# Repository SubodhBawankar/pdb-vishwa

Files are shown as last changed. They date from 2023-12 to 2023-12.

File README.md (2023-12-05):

# pdb-vishwa
# Power Distribution Board for Vishwa Rover 2024

The circuitry converts voltage from batteries to a specific voltage using voltage regulators and switching regulators. Adjustable voltage converters are used to convert 12V to 5V, 3.7V, and 3.3V. Switching buck-boost converters are used to obtain 7V, 9V, and 24V from 12V. All this circuitry is integrated into a single Printed Circuit Board.

[Components List](https://docs.google.com/spreadsheets/d/1e5Fw-HEnwtgFm58ctA9HxLs7_NTRD_BNhpObLu1VbHM/edit?usp=sharing)

### Images: 
Connections:

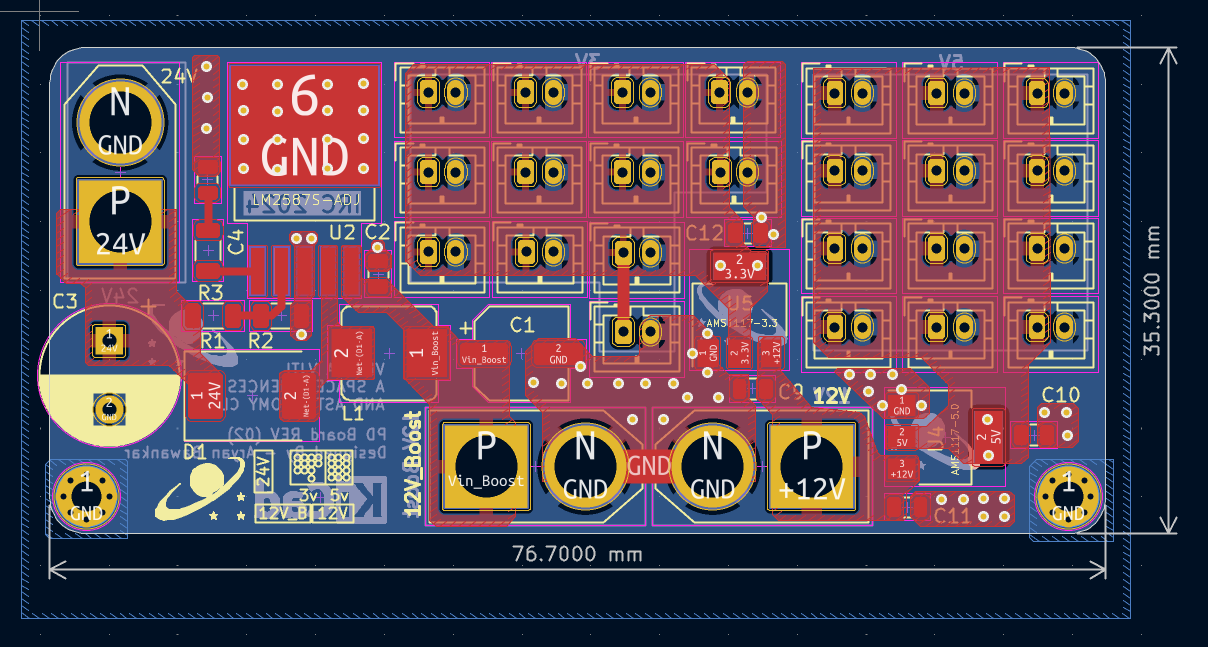
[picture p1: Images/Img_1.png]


3D View:

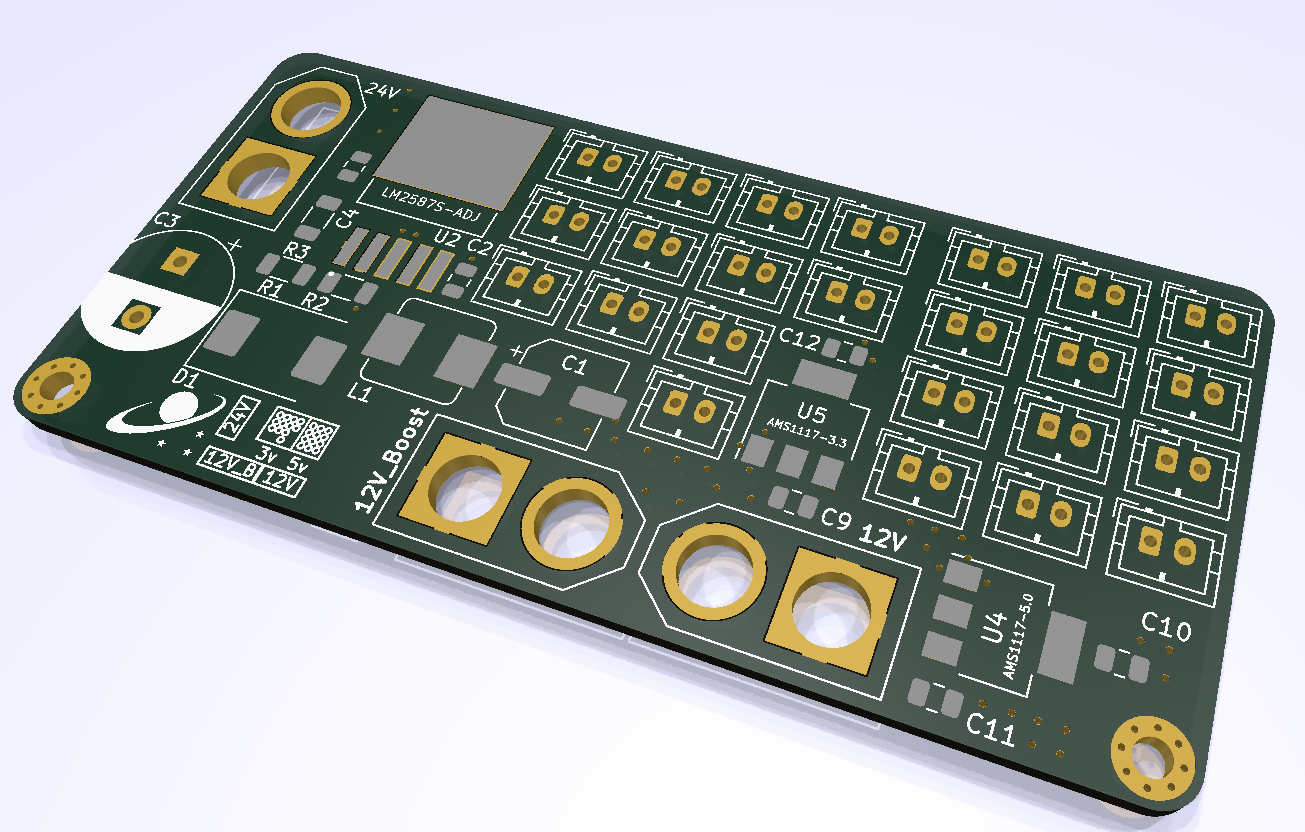
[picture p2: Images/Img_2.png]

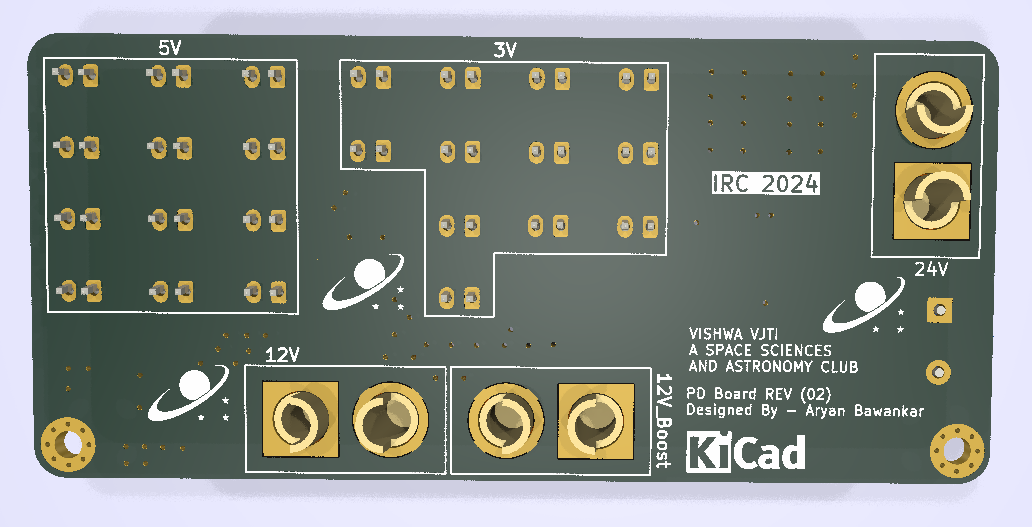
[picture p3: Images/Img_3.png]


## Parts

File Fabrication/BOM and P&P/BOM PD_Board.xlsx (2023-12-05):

Comment | Designator | Footprint | Quantity | JLCPCB Part # | Digikey Mgf #
2k | R2 | R_1206_3216Metric | 1 | C17944 | ESR18EZPF2001
33uH | L1 | L_Bourns_SRP7028A_7.3x6.6mm | 1 | C2046760 | SRP7028A-330M
36.9k | R1 | R_1206_3216Metric | 1 | C205346 | RC1206FR-0736K5L
AMS1117-3.3 | U5 | SOT-223-3_TabPin2 | 1 | C5250992 | 4518-AMS1117-3.3CT-ND
0.1uF | C2 | C_0805_2012Metric | 1 | C6641151 | C2012X7T2E104K125AE
0.68uF | C4 | C_0805_2012Metric | 1 | C520000 | C0805C684K5RAC7800
100uF | C1 | CP_Elec_6.3x7.7 | 1 | C5253633 | UCL1V101MCL6GS
1000uF | C3 | CP_Radial_D10.0mm_P5.00mm | 1 | C136014 | 35PX1000MEFC10X20
MBR745 | D1 | D_SMC | 1 | C524830 | SK56L-TP
10 uF | C11,C9,C10,C12 | C_0805_2012Metric | 4 | C162422 | GRM21BR61E106KA73L
3k | R3 | R_1206_3216Metric | 1 | C205286 | RC1206JR-073KL
AMS1117-5.0 | U4 | SOT-223-3_TabPin2 | 1 | C347223 | AZ1117IH-5.0TRG1
LM2587S-ADJ | U2 | VREG_TPS79625KTTR | 1 | C1355343 | LM2587SX-ADJ/NOPB
B2B-PH-K | P16,P19,P7,P24,P26,P13,P17,P21,P25,P23,P4,P22,P14,P28,P27,P2,P1,P5,P18,P3,P15,P20,P8,P6 | JST_PH_B2B-PH-K_1x02_P2.00mm_Vertical | 24 | C131337 | B2B-PH-K-S
XT60PW-M | J1,J2,J7 | AMASS_XT60-M | 3 | C98733 | PRT-10474
MountingHole_Pad | H2,H1 | MountingHole_2.2mm_M2_Pad_Via | 2

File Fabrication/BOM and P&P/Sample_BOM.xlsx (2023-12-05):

Comment | Designator | Footprint | JLCPCB Part #（optional）
100uF | C1 | CAP-SMD_L3.5-W2.8 | C16133
15K | R5,R6 | R0603 | C22809
DC-005-20A_C136744 | DC1 | DC-IN-TH_DC-005-20A | C136744
Header-Female-2.54_1x8 | P2,P3 | HDR-TH_8P-P2.54-V | C27438
K2-1102DP-C4SW-04 | SW1 | KEY-TH_4P-L6.0-W6.0-P4.50-LS6.5 | C110153
ATMEGA328P-PU | U1 | DIP-28_L34.6-W7.3-P2.54-LS10.2-BL | C33901
670688000 | USB1 | USB-B-TH_67068-8000 | C114097

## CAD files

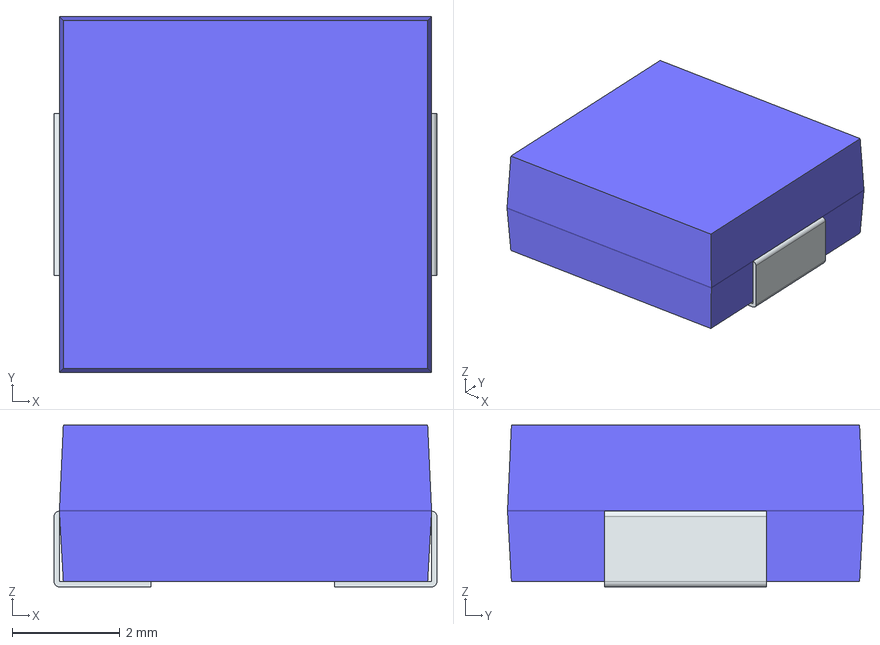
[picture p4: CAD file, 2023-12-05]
comps/22uH_IND/SRP7028AA-150M.stp
7.10 x 6.60 x 3.00 mm
FilletPin1
FilletPin2

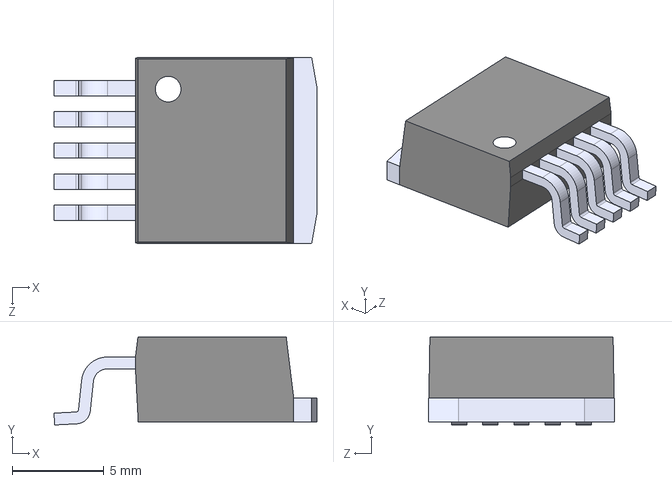
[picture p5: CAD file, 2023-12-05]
comps/LM2587S-ADJ/LM2587S-ADJ.step
14.4 x 4.80 x 10.2 mm

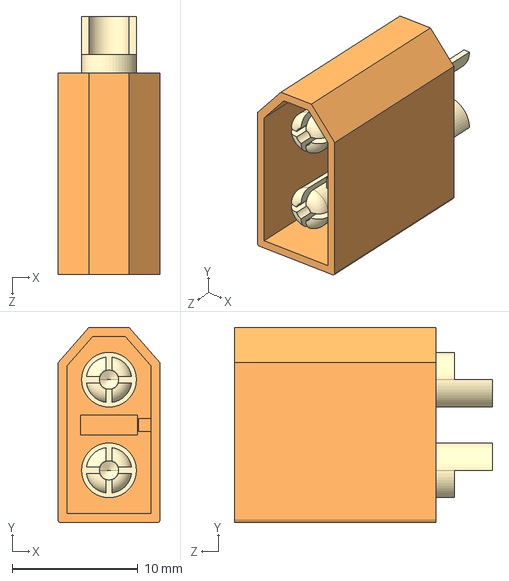
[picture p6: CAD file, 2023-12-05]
comps/XT60-M/XT60-M.step
8.10 x 15.5 x 20.5 mm

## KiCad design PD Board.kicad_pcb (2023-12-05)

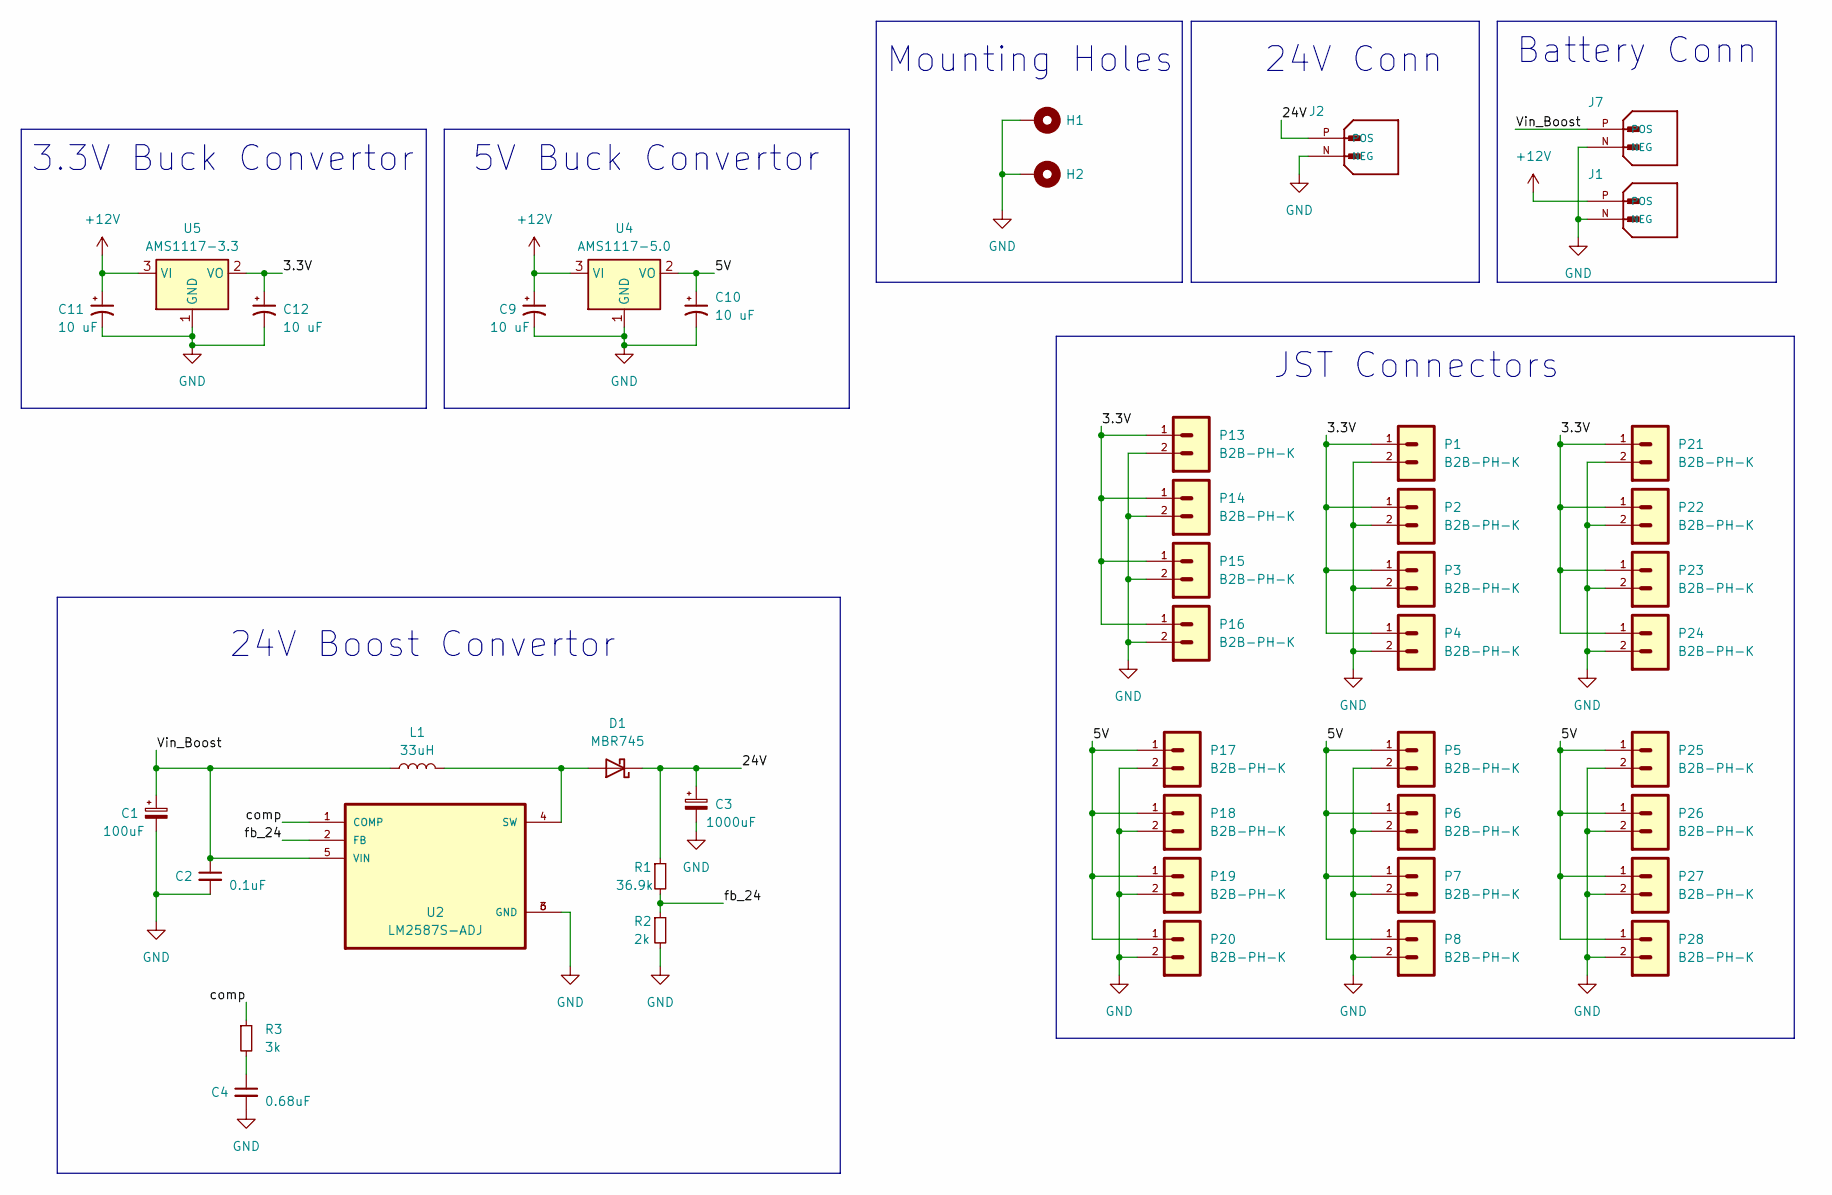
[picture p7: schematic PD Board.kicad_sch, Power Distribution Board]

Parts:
C1: 100uF; CP_Elec_6.3x7.7
C2: 0.1uF; C_0805_2012Metric
C3: 1000uF; CP_Radial_D10.0mm_P5.00mm
C4: 0.68uF; C_0805_2012Metric
C9, C10, C11, C12: 10 uF; C_0805_2012Metric
D1: MBR745; D_SMC
H1, H2: MountingHole_Pad; MountingHole_2.2mm_M2_Pad_Via
J1, J2, J7: XT60PW-M; AMASS_XT60-M; PARTREV V1.2
L1: 33uH; L_Bourns_SRP7028A_7.3x6.6mm
P1, P2, P3, P4, P5, P6, P7, P8, P13, P14, P15, P16, P17, P18, P19, P20, P21, P22, P23, P24, P25, P26, P27, P28: B2B-PH-K; JST_PH_B2B-PH-K_1x02_P2.00mm_Vertical
R1: 36.9k; R_1206_3216Metric
R2: 2k; R_1206_3216Metric
R3: 3k; R_1206_3216Metric
U2: LM2587S-ADJ; VREG_TPS79625KTTR
U4: AMS1117-5.0; SOT-223-3_TabPin2
U5: AMS1117-3.3; SOT-223-3_TabPin2

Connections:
+12V: C9.1, C11.1, J1.P (POS), U4.3 (VI), U5.3 (VI)
/3.3V: C12.1, P1.1, P2.1, P3.1, P4.1, P13.1, P14.1, P15.1, P16.1, P21.1, P22.1, P23.1, P24.1, U5.2 (VO)
/5V: C10.1, P5.1, P6.1, P7.1, P8.1, P17.1, P18.1, P19.1, P20.1, P25.1, P26.1, P27.1, P28.1, U4.2 (VO)
/24V: C3.1, D1.1 (K), J2.P (POS), R1.1
/Vin_Boost: C1.1, C2.1, J7.P (POS), L1.1, U2.5 (VIN)
/comp: R3.1, U2.1 (COMP)
/fb_24: R1.2, R2.1, U2.2 (FB)
GND: C1.2, C2.2, C3.2, C4.2, C9.2, C10.2, C11.2, C12.2, H1.1, H2.1, J1.N (NEG), J2.N (NEG), J7.N (NEG), P1.2, P2.2, P3.2, P4.2, P5.2, P6.2, P7.2, P8.2, P13.2, P14.2, P15.2, P16.2, P17.2, P18.2, P19.2, P20.2, P21.2, P22.2, P23.2, P24.2, P25.2, P26.2, P27.2, P28.2, R2.2, U2.3 (GND), U2.6 (GND), U4.1 (GND), U5.1 (GND)
unnamed: C4.1, R3.2
unnamed: D1.2 (A), L1.2, U2.4 (SW)

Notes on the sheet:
Battery Conn
24V Conn
5V Buck Convertor
Mounting Holes
JST Connectors
24V Boost Convertor
3.3V Buck Convertor

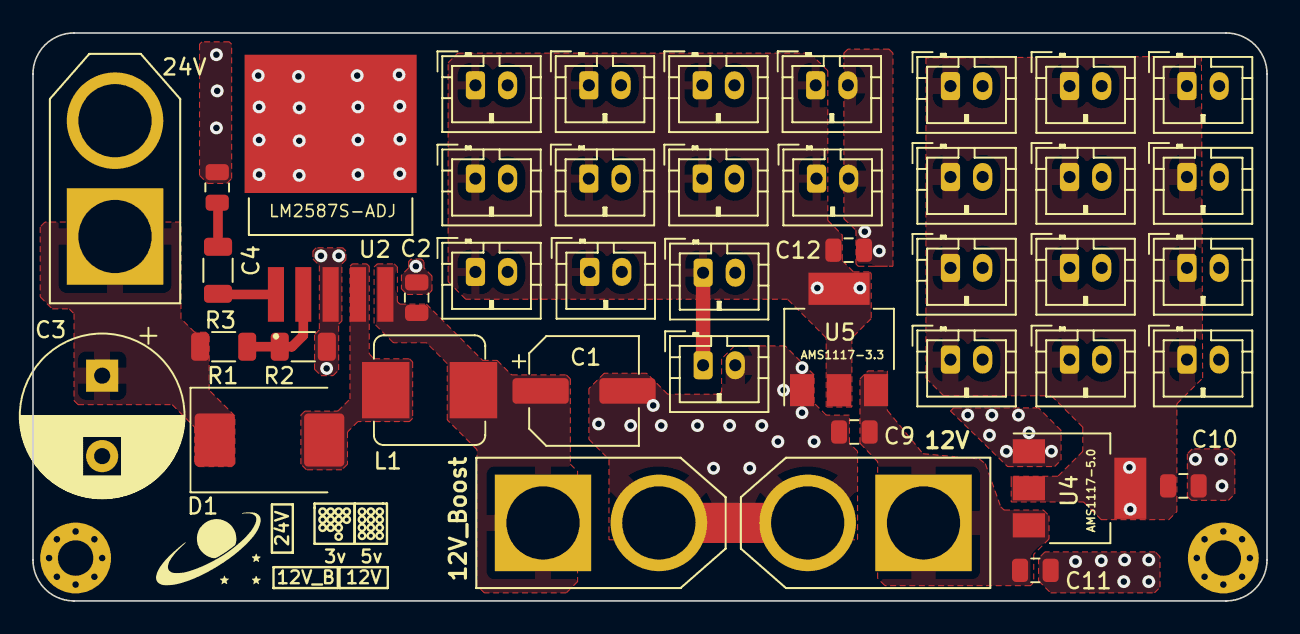
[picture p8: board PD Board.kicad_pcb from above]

Board: 2 copper layers, 76.7 x 35.3 mm, 45 parts (0 on the bottom side), 10 nets.

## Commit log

2023-12-05 Deleting Old Files
    [PD Board.kicad_pcb, PD Board.kicad_sch]
2023-12-05 Final Board Upload
    [BOM PD_Board.xlsx, LM2587S-ADJ.step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]
